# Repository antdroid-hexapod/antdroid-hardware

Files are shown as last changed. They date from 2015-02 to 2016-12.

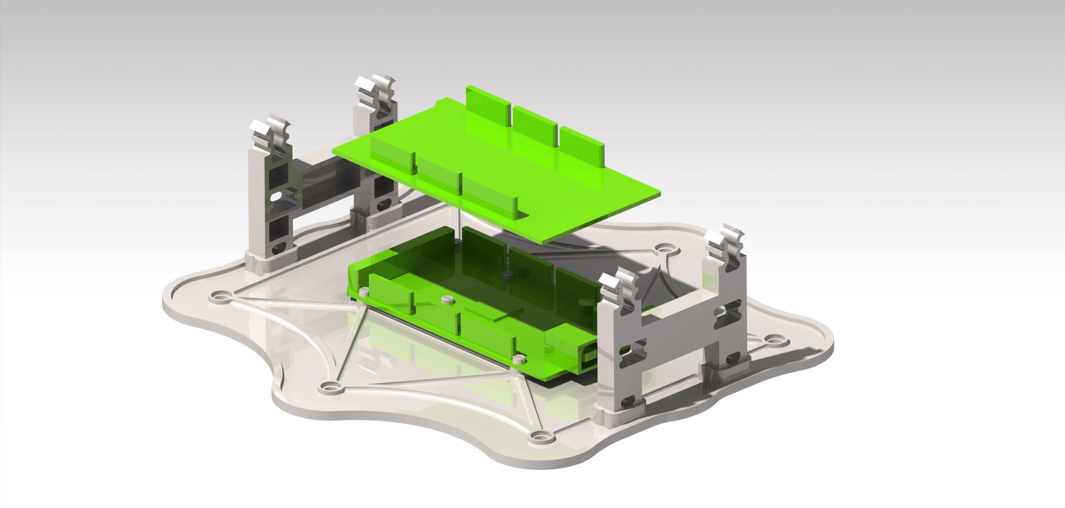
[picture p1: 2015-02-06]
assembly/Body assembly/02 - Arduino + protoshiel.jpg

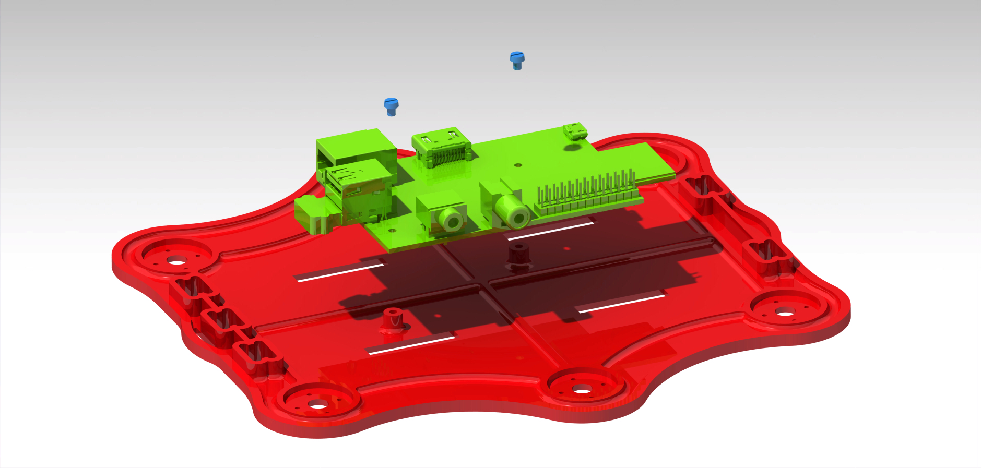
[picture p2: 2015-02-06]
assembly/Body assembly/03 - top base + RPI.jpg

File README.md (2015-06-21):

#Antdroid Hardware Components
Antdroid is a robot designed to be 3D printed.

It is ***designed in CATIA  V5r21*** with a ***full parametric design***, witch allows you to easily ***resize and adapt*** the model to your own servos or hardware requirements.

Unfortunately, CATIA is not a free opensource program, so if you want to modify it, you will need a license. We would like to port it to a free software solution but, at the moment, it is not posible.

## 3D printable parts
All the parts have been exported to ***stl format***, so you can easily print them.

### Recommendations for printing
| Part | Layer Height | Infill | Support  | Number of Pieces | Plastic (g) | Material |
|---|---|---|---|---|---|---|
| Coxa | 0.2 | 40%  | Yes | 6 | 189 | PLA |
| Femur | 0.25 | 40%  | No | 6 | 30 | PLA or ABS |
| Femur simetria | 0.25 | 40%  | No | 6 | 30 | PLA or ABS |
| Separador | 0.2 | 40%  | No | 6 | 9 | PLA |
| Tibia | 0.2 | 40%  | Yes | 6 | 342 | PLA |
| Tapa servo | 0.1 | 50%  | Yes | 18 | 128 | PLA or ABS |
| Base inferior | 0.2 | 25%  | No | 1 | 156 | PLA |
| Base superior | 0.2 | 25%  | No | 1 | 158 | PLA |
| Separador cuerpo | 0.2 | 40%  | No | 2 | 19 | ABS |
| Soporte camara | 0.2 | 40%  | No | 1 | 20 | ABS |
| Pie | | | Yes | 6 | | |

## Nuts and bolts

| Nuts and bolts 	| Number 	|
|---	|---	|
| Countersink screw M2.5x20 	| 13 	|
| Countersink screw M3x16 	| 6 	|
| Screw M3x20 	| 74 	|
| Nut M3 	| 8 	|
| Washer M3 	| 18 	|
| Countersink screw 2.2x6.5 	| 72 	|

## Vitamins

| Component 	| Number 	|
|---	|---	|
| Towerpro MG996R 10kg Servo 	| 18 	|
| Lipo Battery (2S or above) 	| 1 	|
| XT60 Connector (Male) 	| 1 	|
| YEP 20A SBEC 	| 1 	|
| Arduino Mega 2560 r3 	| 1 	|
| Arduino Mega Proto Shield R3 	| 1 	|
| Male Pin Strip 0.1'' 	| 60 	|
| DC 7V-24V To DC 5V 3A USB 	| 1 	|
| Raspberry Pi Model B 	| 1 	|
| 8GB SD Card 	| 1 	|
| USB Wifi 	| 1 	|
| Raspberry Pi Camera Board 	| 1 	|

***WARN***: To date, Raspberry Pi(RPi) B+ and RPi 2 have been released. Due to design specifications, the ***AntDroid frame can ONLY hold RPi B (NOT model B+)***. This is due to the place of the holes that the RPi board have. In fact, RPi B+ and RPi 2 have more holes (4 instead 2). In future upgrades we are going to fix this problem releasing a base to hold the new RPi. Meanwhile, ***RPi B+ is not supported***.
***NOTE***: Now we added a new base to ***support RPi 2***.

Optional

| Component 	| Number 	|
|---	|---	|
| LiPo low voltage alarm | 1 	|
| PS3 Dualshock controller | 1 	|
| USB Bluetooth | 1 	|
| USB hub external power supply | 1 	|

***WARN***: The SBEC doesn't alert of a low battery charge. It is highly recommendable to add a voltage alarm to the LiPo battery in order to not damage it.

The Raspberry Pi B has only two USB ports. One of them is going to be used by the serial connection with the Arduino MEGA. This fact leaves us two connectivity options:

  Bluetooth
  
  Wifi

If you want to use them at the same time you will have to buy a USB hub with external power supply because the RPi can not power several devices with a high power consumption.

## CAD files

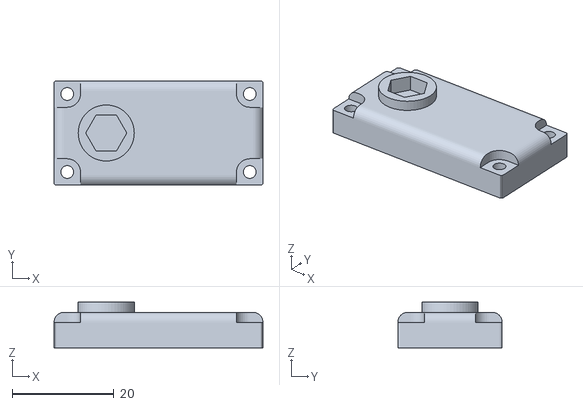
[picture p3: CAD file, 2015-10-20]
stl/996R/Tapa servo.stl
41.0 x 20.5 x 9.00

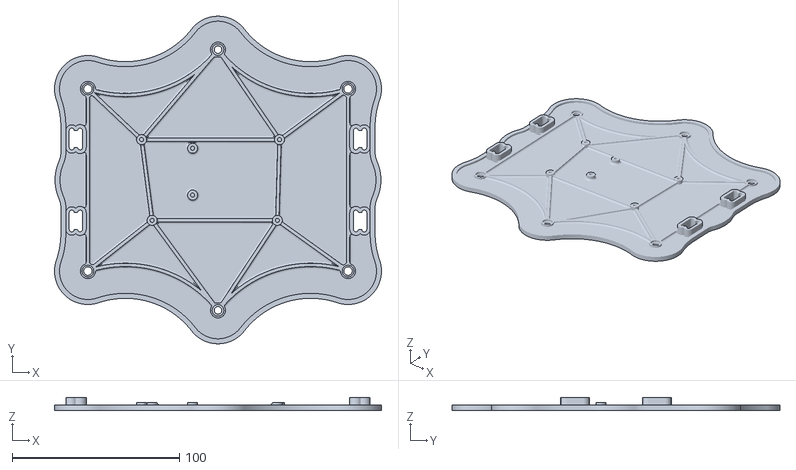
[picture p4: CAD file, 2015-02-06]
stl/body/bottom base.stl
195.6 x 196.0 x 8.00

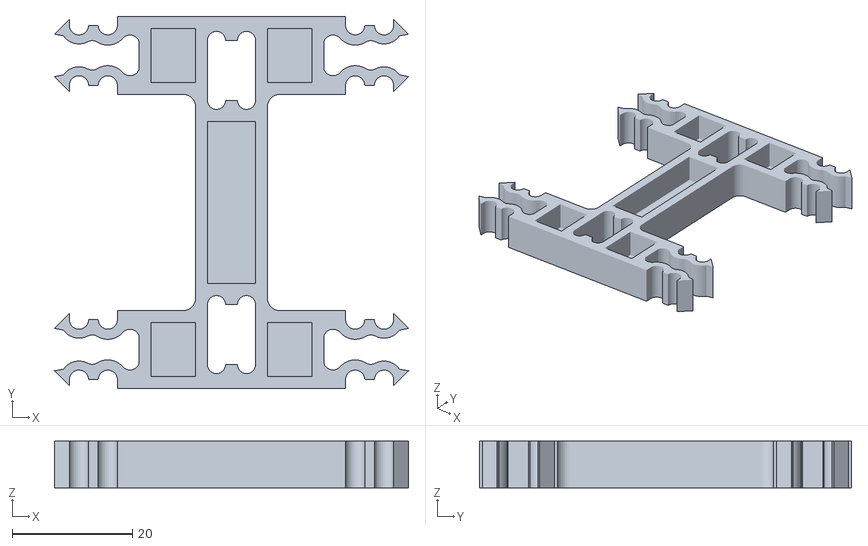
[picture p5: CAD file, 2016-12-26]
stl/cuerpo/Separador cuerpo.stl
58.9 x 62.0 x 7.80

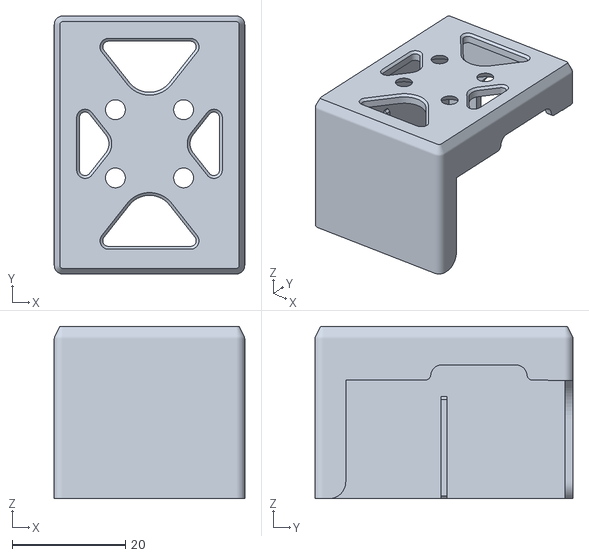
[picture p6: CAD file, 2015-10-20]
stl/Gimbal/gopro1_2_box.STL
33.6 x 45.5 x 30.4

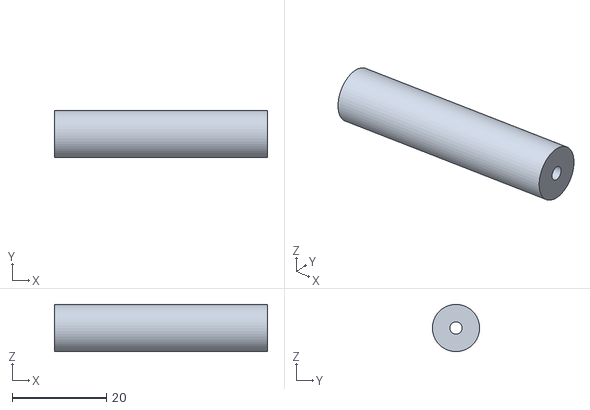
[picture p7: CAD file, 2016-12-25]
stl/pata/Separador.stl
45.1 x 10.0 x 9.98

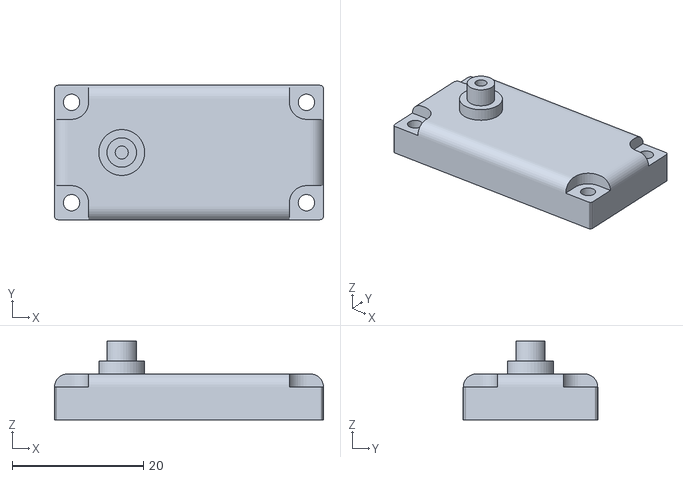
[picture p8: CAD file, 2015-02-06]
stl/996R/servo case.stl
41.0 x 20.5 x 12.0

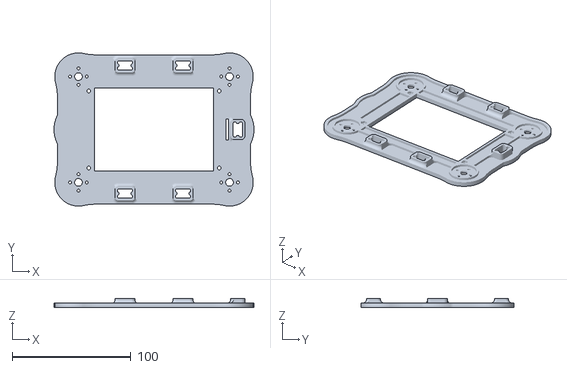
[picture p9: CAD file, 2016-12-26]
stl/cuerpo/Base superior tetrapodo.stl
168.7 x 129.2 x 8.00

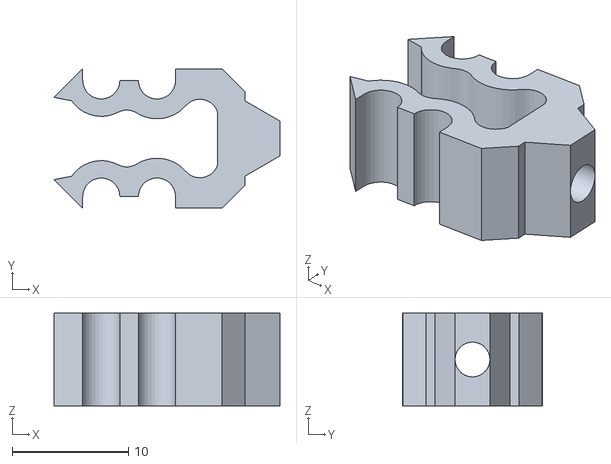
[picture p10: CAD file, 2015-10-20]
stl/Gimbal/separador 2.stl
19.5 x 12.0 x 8.00

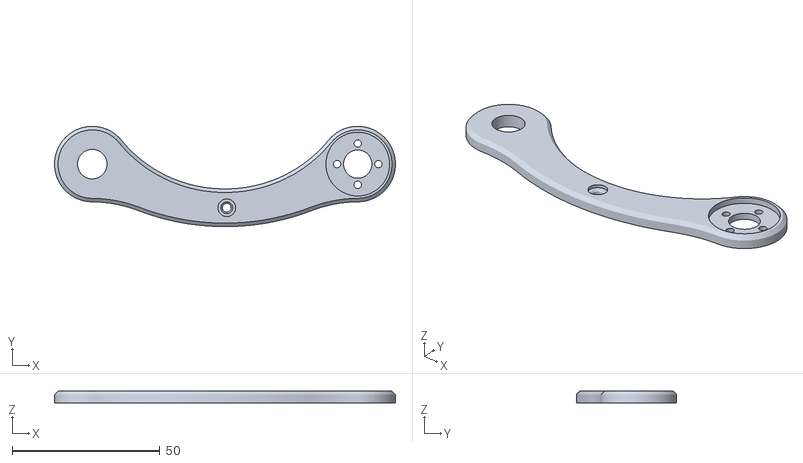
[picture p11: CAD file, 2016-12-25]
stl/pata/Femur.stl
115.6 x 34.0 x 4.00

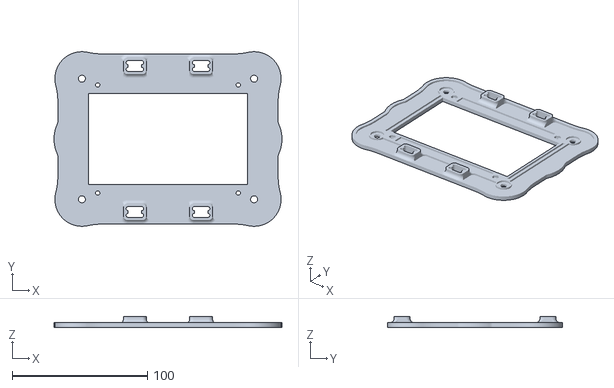
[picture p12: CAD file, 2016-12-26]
stl/cuerpo/Base inferior tetrapodo.stl
168.7 x 129.2 x 8.00

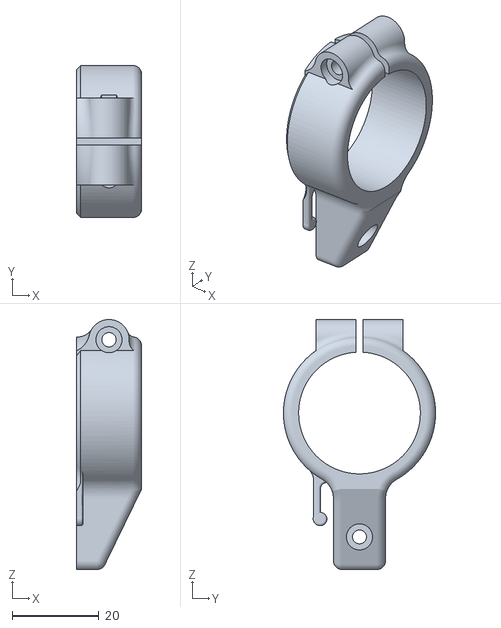
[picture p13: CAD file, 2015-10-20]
stl/Gimbal/arm1.STL
15.0 x 35.0 x 57.5

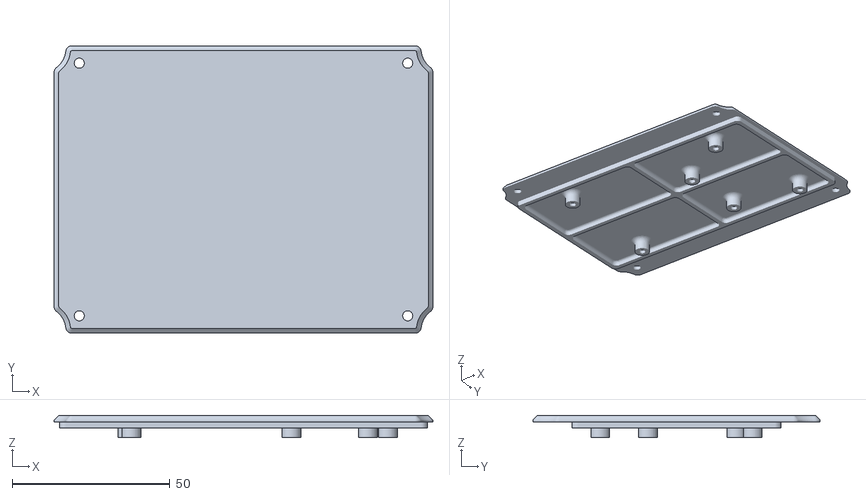
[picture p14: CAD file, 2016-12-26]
stl/cuerpo/Tapa base inferior.stl
120.0 x 91.0 x 7.00

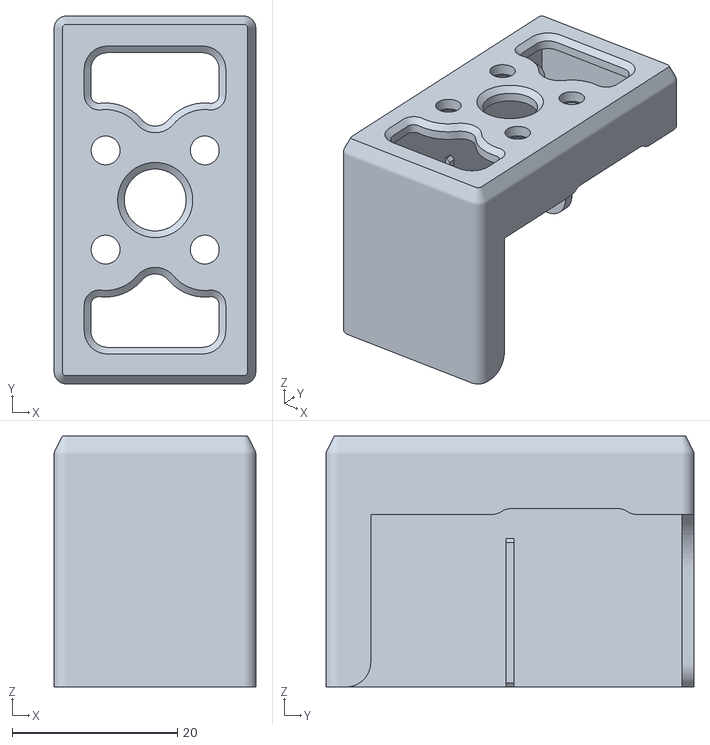
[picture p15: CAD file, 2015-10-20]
stl/Gimbal/gopro3_box.STL
24.5 x 44.6 x 30.4

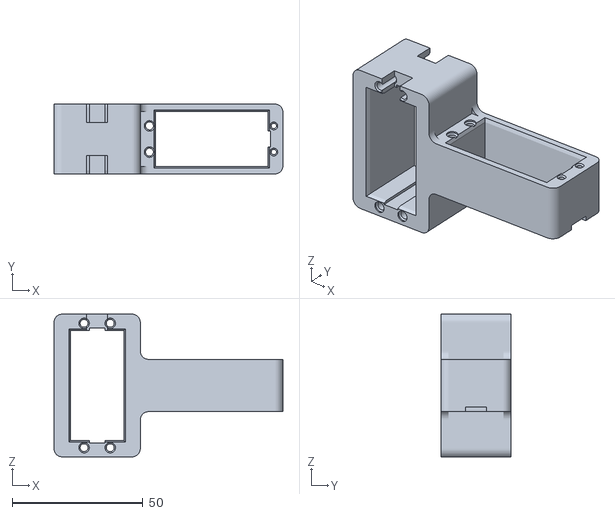
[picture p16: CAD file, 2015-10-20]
stl/pata/Coxa.stl
87.5 x 26.7 x 54.5

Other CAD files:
stl/pata/Femur simetria.stl
stl/cuerpo/Tapa base superior.stl
stl/Gimbal/suspension frame 3.stl
stl/cuerpo/Soporte camara.stl
src/Antdroid.CATProduct
src/Cabeza/Vector_Concept_Robot_ARM_CLAW_standard_servo/Finger.CATPart
src/Cabeza/Vector_Concept_Robot_ARM_CLAW_standard_servo/Product1.CATProduct
src/Cabeza/Vector_Concept_Robot_ARM_CLAW_standard_servo/Top plate.CATPart
src/Cabeza/Vector_Concept_Robot_ARM_CLAW_standard_servo/arm-bottom-plate.CATPart
src/Cabeza/Vector_Concept_Robot_ARM_CLAW_standard_servo/arm-link.CATPart
src/Cabeza/Vector_Concept_Robot_ARM_CLAW_standard_servo/arm-top-plate.CATPart
src/Cabeza/Vector_Concept_Robot_ARM_CLAW_standard_servo/gear-link-12.CATPart
src/Cabeza/Vector_Concept_Robot_ARM_CLAW_standard_servo/gear-link-22.CATPart
src/Electronica/Arduino Mega 2560/Arduino Mega.CATPart
src/Electronica/Arduino Mega 2560/Arduino.CATProduct
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

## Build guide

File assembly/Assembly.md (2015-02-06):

# Assembly

Do you have a bunch of printed pieces on your table and you don't know what to do with them? Don't worry, you are in the correct place. In this folder you will find a lot of pictures and usefull tips and tricks to assembly your own AntDroid (without breaking anything).

## First step
The first thing you should check is how to modify your boring MG 996 servos adding them a new top case. We suggest you how to do it in the "Servo assembly" folder.

## Legs
In the "Leg assembly" folder you will find how to assembly one leg. The tutorial includes mounting the frame and the servos that it holds.

## Body
The last step of this little assembly tutorial is the assembly of the body. In the "Body assembly" folder you will find the last step of the assembly manual in which the top and bottom bases will be assembled.

## Pin
(Work in progress)

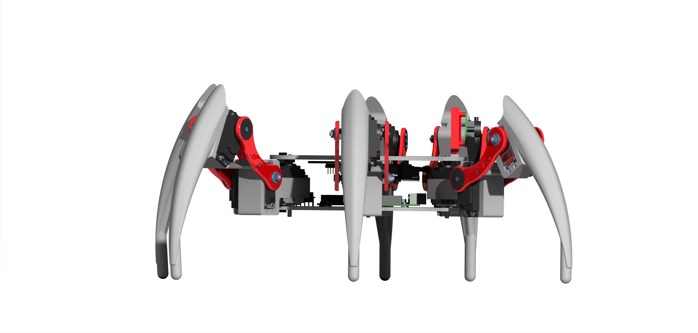
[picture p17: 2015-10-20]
render/assembly/profile.jpg

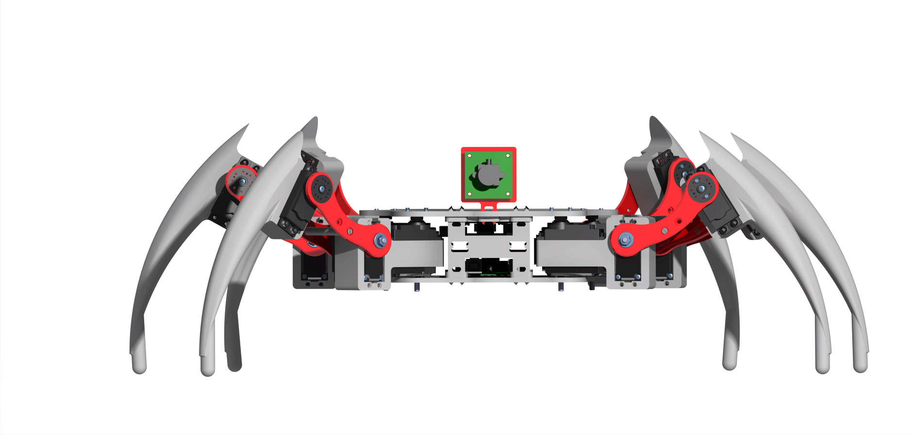
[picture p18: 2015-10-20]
render/assembly/elevation.jpg

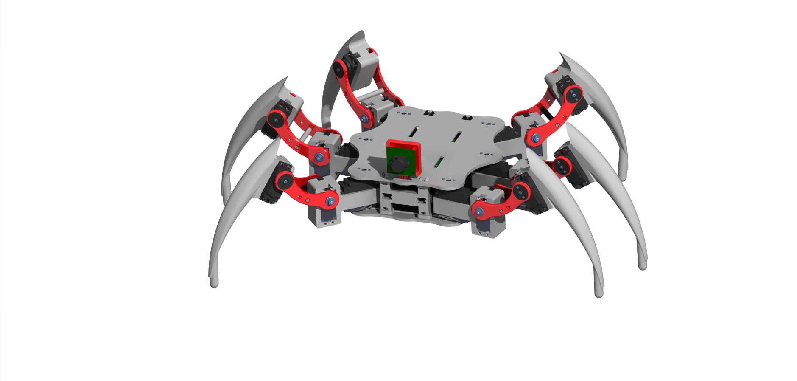
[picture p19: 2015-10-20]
render/assembly/isometric3.jpg

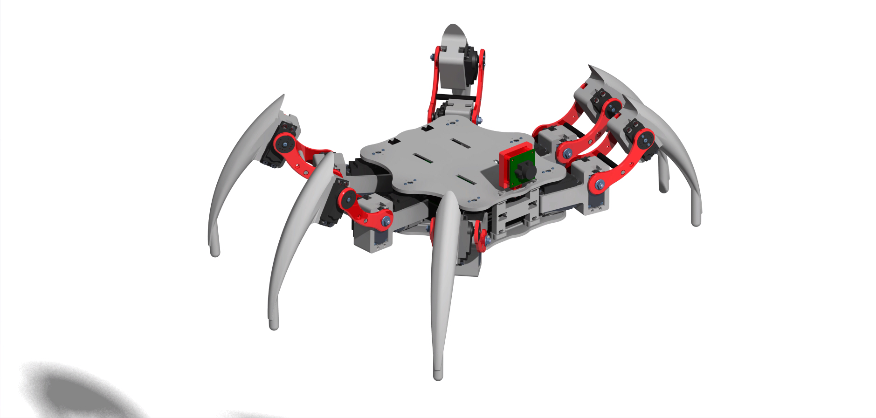
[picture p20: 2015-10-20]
render/assembly/isometric4.jpg

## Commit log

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2015-02-06 stl: the stl files have been translated from spanish to english.
    [Base inferior.stl, Coxa.stl, Femur_lateral.stl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]
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2015-02-06 Separador is now separador cuerpo
    [Separador cuerpo.stl]
2015-02-12 New stl of coxa
    [Coxa.stl]
2015-06-19 Added base superior RPI2.
    A new upper case has been added. It can hold the new Raspberry Pi 2.
    [Base superior RPI2.CATPart]
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2015-08-01 Tapa servo: removed plastic shaft.
    Deleted old plastic shaft. Added groove for a hexagonal M4x12 bolt, which will
    be the new metalic shaft.
    [Tapa servo.CATPart]
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2015-08-01 Added M4x8 bolt to servo assembly.
    [Tapa servo.CATPart, servo 996r_MODIFICADO.CATProduct]
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2015-08-01 Femur_lateral: new hole for 4x10x4 bearing.
    [Femur_lateral.CATPart]
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2015-08-01 Added 2 bearing 4x10x4 to pata assembly.
    [Pata.CATProduct, servo 996r_MODIFICADO.CATProduct]
2015-08-01 Femur: more support material for a better seating of the bearing.
    [Femur_lateral.CATPart]
2015-08-01 Fixed bug
    [Femur_lateral.CATPart, Pata.CATProduct, Tapa servo.CATPart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]
2015-08-01 Added M4 washer to pata assembly.
    [ISO_7093_1_4x12_STEEL_GRADE_A_LARGE_SERIES_PLAIN_WASHER.CATPart, Pata.CATProduct, servo 996r_MODIFICADO.CATProduct]
2015-08-01 Added M4 nut to Pata aseembly.
    [ISO_4032_M4_STEEL_GRADE_A_HEXAGON_NUT.CATPart]
2015-08-01 Servo: The M4x8 bolt is now a M4x10 bolt.
    [Pata.CATProduct, Tornillo M4x8.CATPart, servo 996r_MODIFICADO.CATProduct]
2015-08-02 Fixed symemetry of femur_lateral.
    [Symmetry of Femur_lateral.CATPart]
2015-08-02 Upgrade of antdroid product.
    [Antdroid.CATProduct, Arduino.CATProduct, Base inferior.CATPart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]
2015-08-02 Base inferior: fixed inner stiffeners.
    [Base inferior.CATPart]
2015-08-02 Deleted old coxa and old tibia.
    [FOOT_TWO.CATPart, UPPER_LEG_LEFT.CATPart]
2015-08-02 Updated base inferior, femur, femur simetria and separador stl files.
    [Femur simetria.stl, Femur.stl, Separador.stl]
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2015-08-02 Added M4 nut and M4 washer to tornilleria folder.
    [ISO_4032_M4_STEEL_GRADE_A_HEXAGON_NUT.CATPart, ISO_7093_1_4x12_STEEL_GRADE_A_LARGE_SERIES_PLAIN_WASHER.CATPart]
2015-08-05 Updated tapa servo stl file.
    [Tapa servo.stl]
2015-08-05 Separador: the 2.5mm drill is now a 3mm drill.
    [Separador2.CATPart]
2015-08-05 femur: the 2.5mm drill for the separador piece is now a 3mm drill.
    [Femur_lateral.CATPart, Pata.CATProduct, Symmetry of Femur_lateral.CATPart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]
2015-08-05 Updated femur and femur simetria stl files.
    [Femur simetria.stl, Femur.stl]
2015-08-05 Updated separador stl file.
    [Separador.stl]
2015-08-08 Added 2 axes gimbal parts, product and stl files.
    [arm1.STL, arm2.STL, brazo 1.CATPart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]
2015-08-10 Deleted gopro1y2.part, separador.part and gimbal.product
    [gopro1y2.CATPart, separador .CATPart]
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2015-08-10 Added separador2 part ans stl files.
    [separador 2 .CATPart, separador 2.stl]
2015-08-10 Added supension_frame_3 part and stl files.
    [suspension frame 3.CATPart, suspension frame 3.stl]
2015-08-10 Gimbal product contains now the new suspension_3 and separador_2 .part files.
    [gimbal.CATProduct]
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2015-08-26 stl files moved from brushless gimbal folder to gimbal folder
    [arm1.STL, arm2.STL, brazo 1.stl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]
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2015-10-20 Removed PINZA and added easy mount feature for servos
    [Antdroid.CATProduct, Coxa.CATPart, Coxa.stl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]
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2015-12-25 Added upper tetrapod case.
    New cover to increase the accesibility to the inner hollow of the robot.
    [Base superior tetrapodo.CATPart, Base superior.CATProduct, ISO_1207_M3x8_STEEL_GRADE_A_SLOTTED_CHEESE_HEAD_SCREW.CATPart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]
2015-12-27 Added base inferior product
    The part files included are:
    - Base inferior tetrapodo
    - Arduino MEGA
    - Tornillo Arduino MEGA x6
    [Arduino Mega.CATPart, Base inferior tetrapodo.CATPart, Base inferior.CATProduct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]
2015-12-27 The stl files below are no longer nedded: - Base inferior.stl (Hexapod) - Base superior RPI2.stl (Hexapod) - Base superior.stl (Hexapod)
2015-12-27 Added cuerpo tetrapodo product
    The part files below have been included in the product
    - Base superior RPI2 tetrapod
    - Base inferior tetrapod
    [Base superior RPI2.CATPart, Base superior.CATProduct, Bearing 4x10x4.CATPart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]
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2016-12-10 Femur lateral: deleted one of the you middle holes. Total length increased from 70 to 90 mm
    [Femur_lateral.CATPart]
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2016-12-10 Separador: Diameter increased from 6 to 10 mm
    [Separador2.CATPart]
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2016-12-10 Symmetry of femur: deleted one of the middle holes. Increased total length from 70 to 90 mm
    [Symmetry of Femur_lateral.CATPart]
2016-12-11 Servo: fixed constrains
    [Tapa servo.CATPart, servo 996r_MODIFICADO.CATProduct]
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2016-12-14 Base inferior: modification of the holes in the base for separador.
    [Base inferior tetrapodo.CATPart, Base inferior.CATProduct]
2016-12-14 Base superior: modification of the holes in the base for separador.
    [Base superior tetrapodo.CATPart, Base superior.CATProduct, Cuerpo.CATProduct]
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2016-12-18 Addded: new part top plate for pinza assembly
    [Top plate.CATPart]
2016-12-18 Pinza: complete rework
    [Finger.CATPart, Product1.CATProduct, arm-link.CATPart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]
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2016-12-25 Tapa base superior: added new stiffener
    [Tapa base superior.CATPart]
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2016-12-26 Base superior: improvement of stiffener
    [Base superior.CATProduct]
2016-12-26 Base superior tetrapodo: improvement of stiffener
    [Base superior tetrapodo.CATPart]
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2016-12-26 Base inferior tetrapodo: new hole for tapa base inferior
    [Base inferior tetrapodo.CATPart]
2016-12-26 Base inferior tetrapodo: new hole for tapa inferior
    [Base inferior tetrapodo.stl]
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2016-12-26 Base superior: diameter of the holes for the horn of the servos increased
    [Base superior tetrapodo.CATPart, Base superior tetrapodo.stl]
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
